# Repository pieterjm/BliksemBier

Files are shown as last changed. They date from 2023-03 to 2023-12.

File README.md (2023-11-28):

# BliksemBier, a Bitcoin Lightning enabled beertap

BliksemBier is a beertap that accepts Bitcoin. BliksemBier consists of two components: na LNbits (https://github.com/lnbits/lnbits) extension and firmware for an ESP32-based smart display (made by Sunton). The firmware for the tap is created in such a way that can be used for different beertap types. For 5L draught kegs to professional beertaps. The following pictures illustrate some of the applications of BliksemBier.

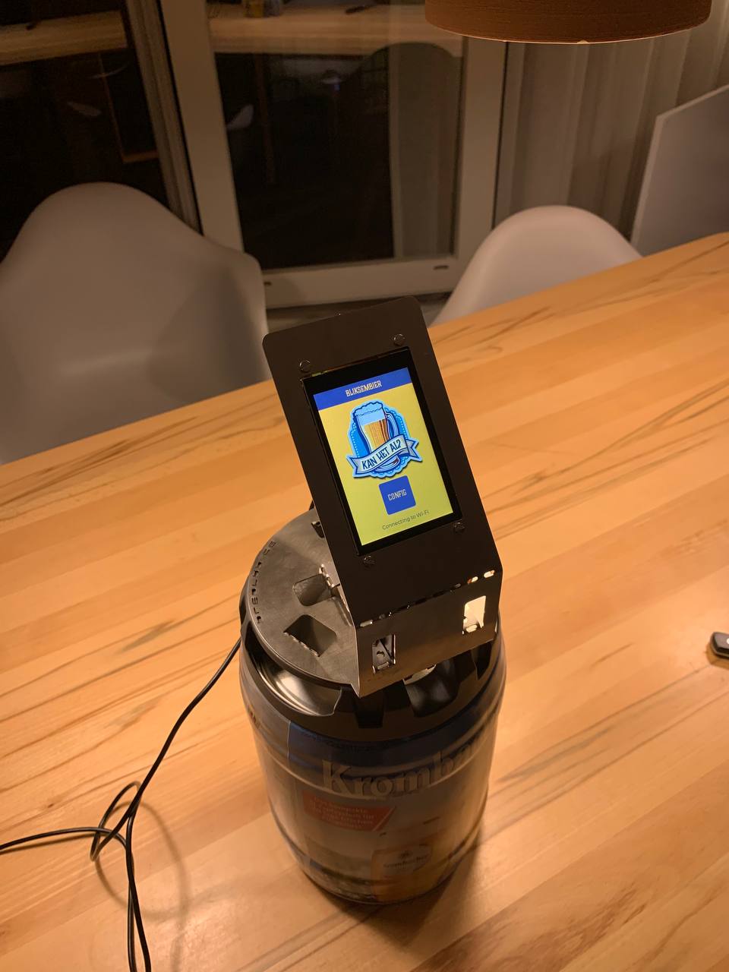
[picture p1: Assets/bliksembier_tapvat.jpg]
Fixture for 5L draught keg
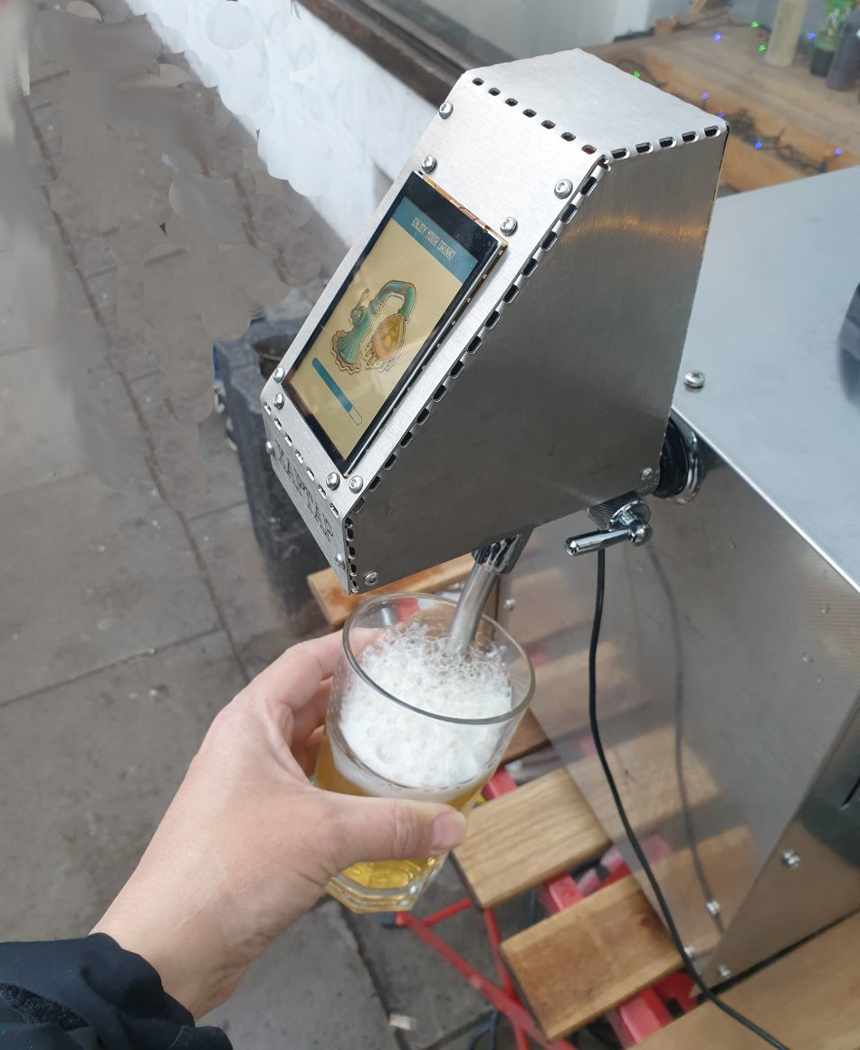
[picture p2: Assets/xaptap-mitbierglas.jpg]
Fixture for a standard beertap, the XapTap made by PlebTap.
 

If you want to obtain or create such a beertap, you can buy one or create one yourself (see the [build instructions](#build-instructions) for more details). All components, except for the metal sheet, are readily available. The design for the metal sheet is available <a href="Hardware/draught_key_sheet_bliksembier.dxf">here</a>. This should be laser cut out of a 1mm - 1.5mm stainless steel sheet. As that can be quite expensive for a few items, you can also obtain one from me. Contact <a href="mailto:bliksembier@meulenhoff.org">me</a> for details.

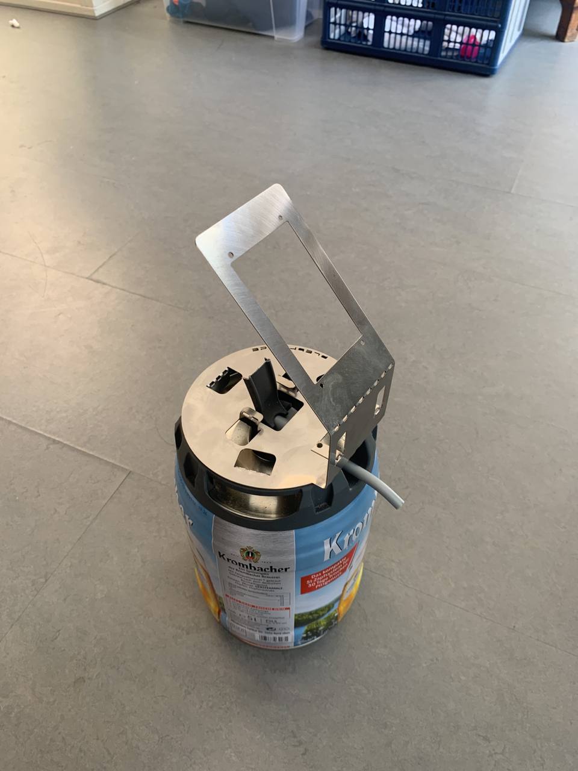
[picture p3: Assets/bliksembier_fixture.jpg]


## Contact, support and licensing

If you want to contact me directly, send an e-mail to <a href="mailto:bliksembier@meulenhoff.org">bliksembier@meulenhoff.org</a>.

You can also join the Telegram group (https://t.me/+NLCoqbPB_ro1NzRk). 

This software is available under the GPL License (see [LICENSE](/LICENSE)). If your application of BliksemBier requires another type of license, contact me by sending an e-mail to <a href="mailto:bliksembier@meulenhoff.org">bliksembier@meulenhoff.org</a>. 

## Installation

To get the beertap up and running, take the following steps:

1. Make sure your LNbits server has the BliksemBier extension installed. If not contact the administrator of your LNbits server and ask to install the BliksemBier extension from the following source:
   ```
   https://lnbits.meulenhoff.org/extensions/extensions.json
   ```
2. In LNbits, add the BliksemBier extension to your wallet.
3. Select the 'BliksemBier' extension and clik the 'New Device' button.
4. Configure the device with a title, wallet, currency and at least one switch (up to three switches are supported). If unsure, no problem, you can change the configuration anytime.
  * The duration is the amount of milliseconds, the tap is switched on.
  * The Label button is displayed on the tap. For instance 'SMALL' or 'LARGE'. Currently, only a limited subset of characters is support (CAPS ONLY).
5. Click 'CREATE DEVICE' and record the ID of the LNURLdevice (8 charachters).

Now move over to the beertap itself. If you need to flash (new) firmware to the device, go to step 12.

6. Power on the beertap and click the 'Config' button.
7. Enter the PIN (the initial PIN is 123456)
8. Configure SSID and Secret to connect the tap to a Wi-Fi network.
9. Make sure that LNbits host is set to: lnbits.meulenhoff.org
10. Set 'Device ID' to the ID of the LNURL device (from step 6). 
11. Click connect. 

If all went as planned, the status says: Wi-Fi connected, Configuration loaded, WebSocket connected and 'Ready to Serve!'. You can click on one of the buttons and scan the QR code. 

The flash new firmware on the device, make sure you are using LNbits with the Chrome (or Edge) browser.

12. Connect the Micro USB port of the ESP32 to your computer.
13. In the BliksemBier extension, select the correct ESP32 board and click the flash button to start the flashing process.
  * In some cases, flashing only works the second time.
  * The 'Boot button' that is mentioned during flashing is typically not required. However, the boot button is located on the back of the ESP32 device (next to the reset button). Pressing both at the same time (while having the ESP32 connected to your computer) usually does the trick.
  
## Required components

A list of components required to build a BliksemBier tap for 5L draught kegs:

  * Sunton ESP32 Capacitive touch display 3.5 inch (https://aliexpress.com/item/1005004632953455.html)
  * One MG995 servo
  * 2 JST 1.25 connectors
  * A stainless sheet fixture
  * USB-C connector for power (https://www.aliexpress.com/item/1005005137763022.html)
  * USB 5V power source of at least 2A @ 5V
  * Some screws and wiring:
    * 4 M3 bolts (20 mm)
    * 4 4mm spacers
    * 8 M3 nuts
    * 1 M4 bolt (15 mm)
    * 1 M4 Locking nut
  * A box for the backside (I used a Strapubox 2515)
  * soldering utensils and a small piece of heat shrink
     
## Build  instructions

Both the ESP32 and the Servo are powered from the 5V source. As the servo is quite strong, a weak power source will result in glitches of the display. Make sure your power source is strong enough. Also it is important not to pass the current for the servo through the ESP32. This means that both the ESP32 and the Servo are directly powered from the same 5V power source. Use the following guidelines to connect everything.

  * The 5V power connects to the VIN of the ESP32 and the power input of the servo (middle cable)
  * The GND of the power input connects to the GND of the ESP32 and the GND of the servo (black cable)
  * Port 21 of the ESP32 connects to the signal input of the servo (Yellow cable).
  * Use the JST connectors to connect both power and signal (PIN 21). 

Connecting everything together may require some soldering and heat shrink. A closeup of the backside should like similar to the following.

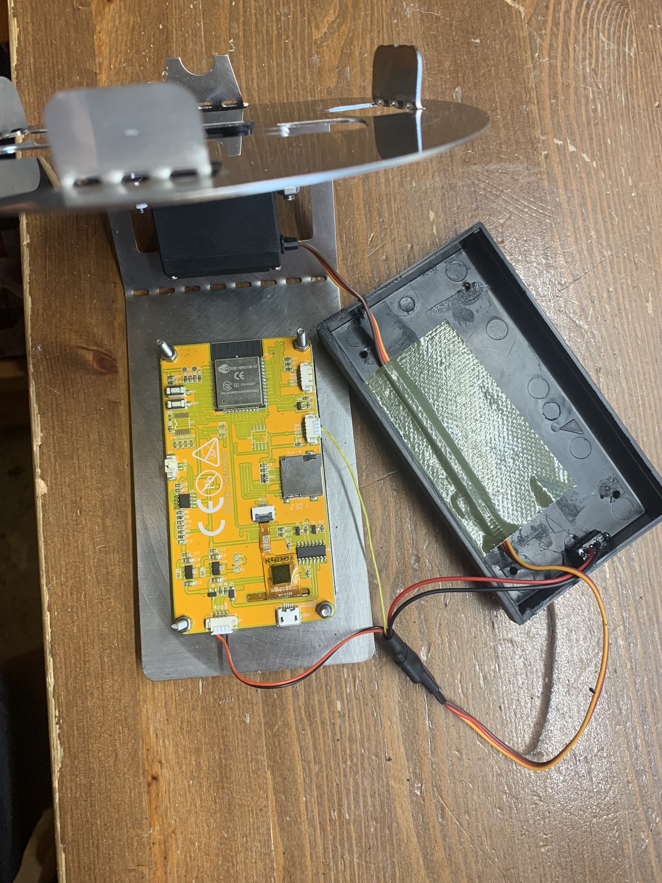
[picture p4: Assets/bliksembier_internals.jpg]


The box for the backside of the tap is a converted strapubox that comes in two identical covers. I cut of the rims of the box, made a hole for the USBC connector and drilled four holes to mount the cover on the same bolts that mount the display to the metal fixture.

## Compilation

To compile the project from within Visual Studio Code using platform.io, take the following steps:

  1. Install Visual Studio Code. Download from https://code.visualstudio.com/. If Git is not yet installed on your system, you need to install that as well.
  2. Install the Platform IO extension. Open the Extension Manager (click the wheel icon at the bottom of the bar and the left and select Extensions). Search for PlatformIO, and click 'Install'.
  3. In Visual Studio code, open the command palette (Ctrl-Shift-P) and type 'gitcl'.
  4. When prompted for the repository URL, enter the URL of this repository: `https://github.com/pieterjm/BliksemBier.git`
  5. Select a local directrory where to store the repository and open the repository.
  6. To compile, click the checkmark icon in the blue bar at the bottom to compile the repository. This may take a while as external libraries have to be loaded.
  7. Connect the device to USB port and click the '>' button in the blue bar at the bottom to compile and flash the firmware.
  8. After compilation and firmware flashing is succesful, the device should restart as a fresh Btap.
  
To compile the project using platformio core only, take the following steps

  1. Install platformio core by following the instructions here: https://docs.platformio.org/en/stable/core/installation/methods/installer-script.html
  2. Clone the repository with the following command
     ```
     git clone https://github.com/pieterjm/BliksemBier.git
     ```
  3. Compile and upload
     ```
     cd BliksemBier
     platformio run --target upload
     ```

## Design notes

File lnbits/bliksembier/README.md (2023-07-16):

# LNURLDevice - <small>[LNbits](https://github.com/lnbits/lnbits) extension</small>
<small>For more about LNBits extension check [this tutorial](https://github.com/lnbits/lnbits/wiki/LNbits-Extensions)</small>

For offline LNURL devices

`Author: Ben Arc` `Author: DNI`

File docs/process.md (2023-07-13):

# Process flow

The global process from startup until making a succesfull payment is depicted in the following figure:

Process flow

The tap is configured with a 'Device ID', which refers to an LNURL device in LNbits. Upon startup the tap retrieves payment configuration from LNbits using this ID. LNbits response with a JSON formatted message that contains all configured Switches, and for each switch, the LNURL and Label. Upon receiving that information, the tap configures buttons and QR codes. Finally a WebSocket connection is opened where the tap listens for incoming messages from LNbits.

When a user wants to order a beer, the desired button is pressed on the tap. This triggers the device to display the appropriate LNURL for the switch.

The user pays for the beer by retrieving an invoice from LNbits and paying the invoice. 

After succesfull payment, a simple text message is sent over the WebSocket. The message is formatted as 'A-B' where A and B are integers. A references the GPIO PIN to be triggered, B is the time (ms) to enable the PIN. So for a larger beer, B should be increased.

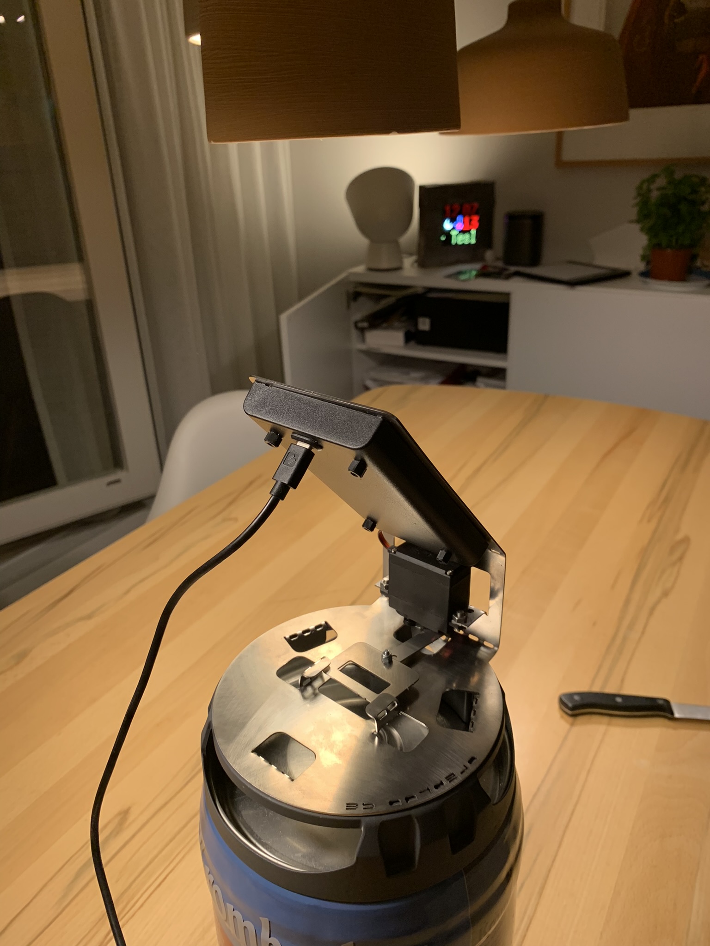
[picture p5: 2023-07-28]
Assets/bliksembier_backside.jpg

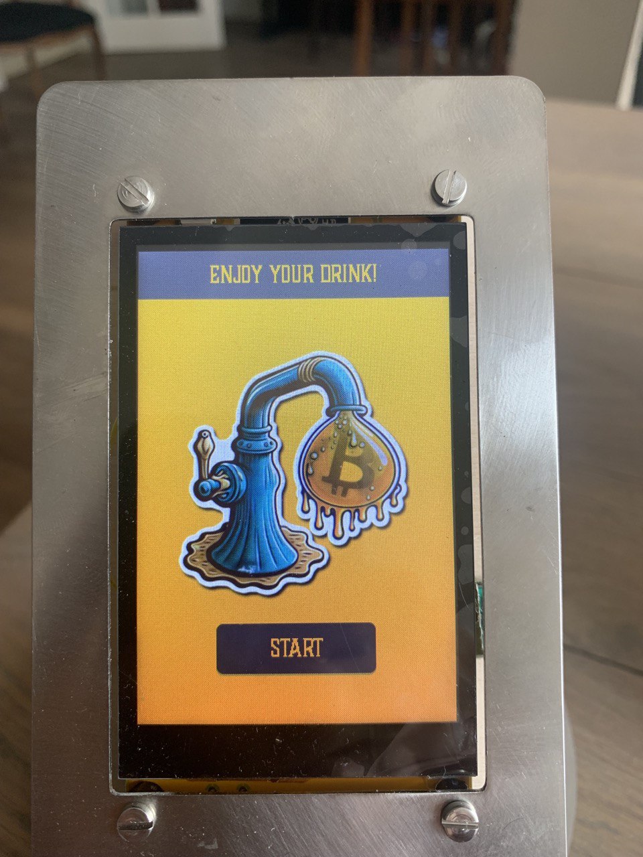
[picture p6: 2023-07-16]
docs/beer.jpg

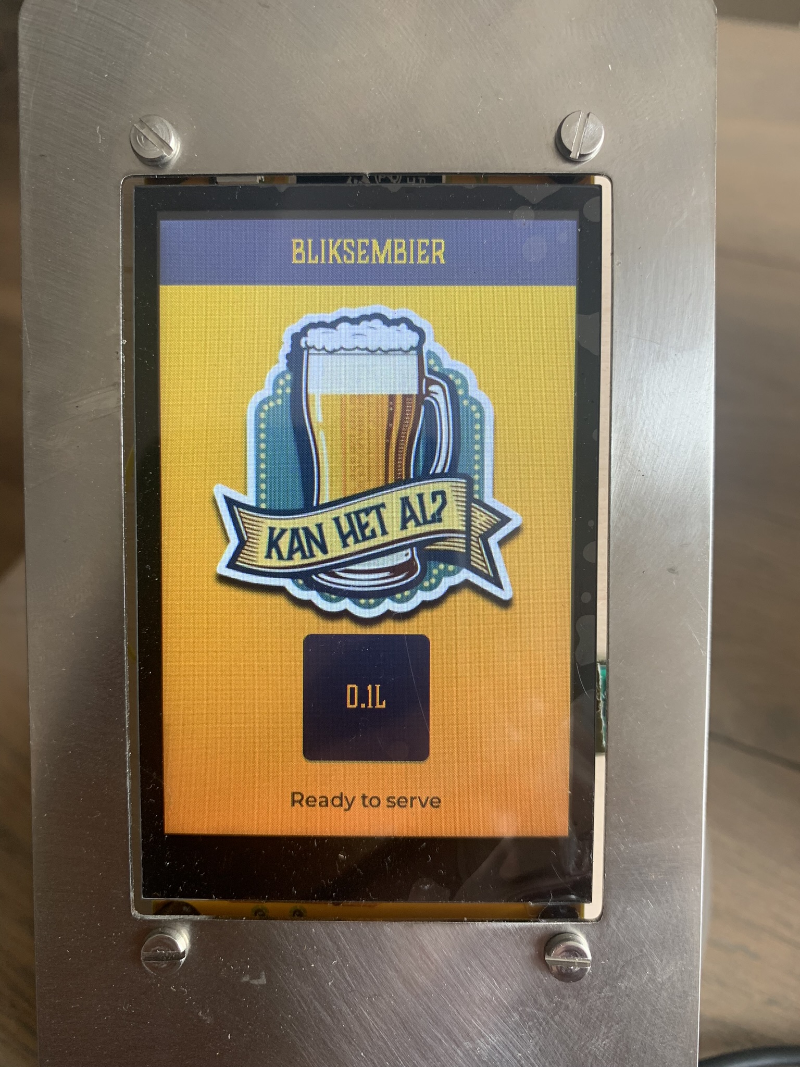
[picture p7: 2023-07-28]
Assets/bliksembier_start_screen.jpg

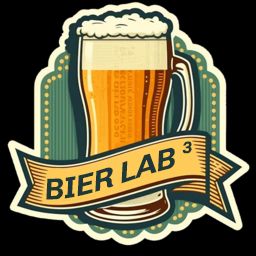
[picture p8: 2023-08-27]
Assets/bliksembier_lab3.jpg

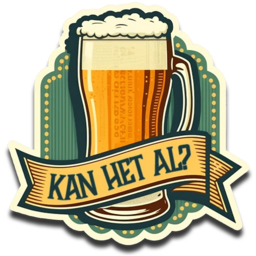
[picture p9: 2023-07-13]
Assets/kanhetal256.png

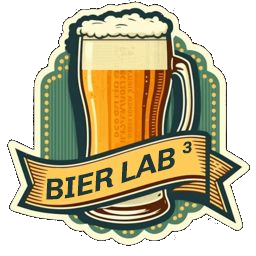
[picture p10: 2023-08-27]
Assets/bliksembier_lab3.png

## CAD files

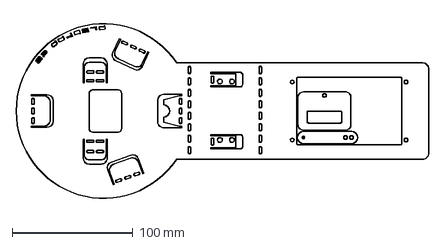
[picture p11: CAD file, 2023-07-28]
Hardware/draught_key_sheet_bliksembier.dxf
342.2 x 157.3 mm

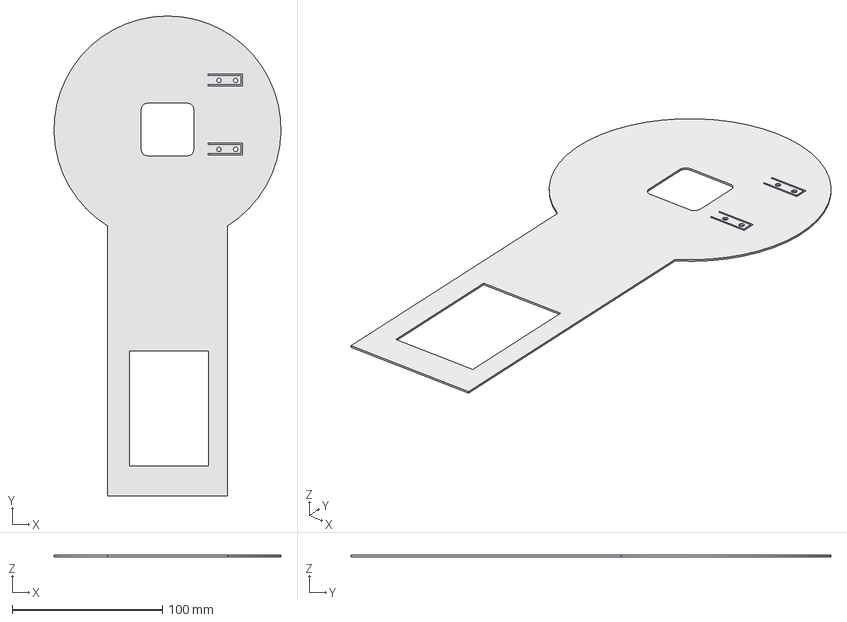
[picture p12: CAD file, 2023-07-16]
Hardware/BliksemBierMetalSheetSketch.FCStd
151.2 x 319.8 x 1.00 mm

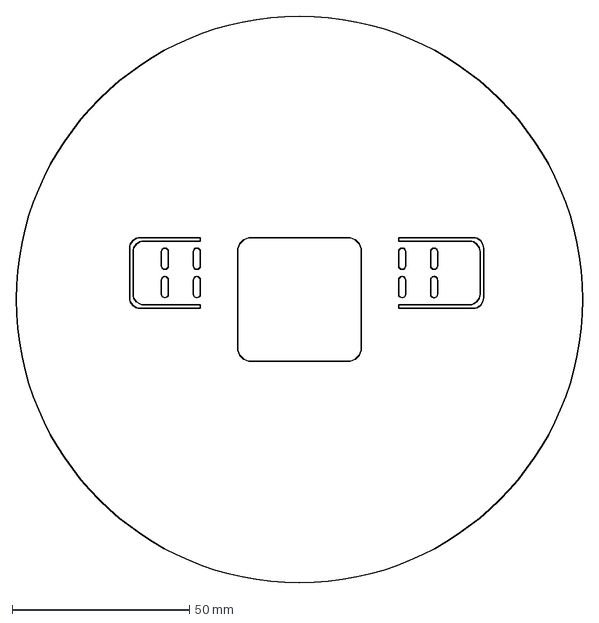
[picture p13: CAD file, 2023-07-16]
Hardware/BliksemBierMetalSheet-Body.dxf
160.0 x 160.0 mm

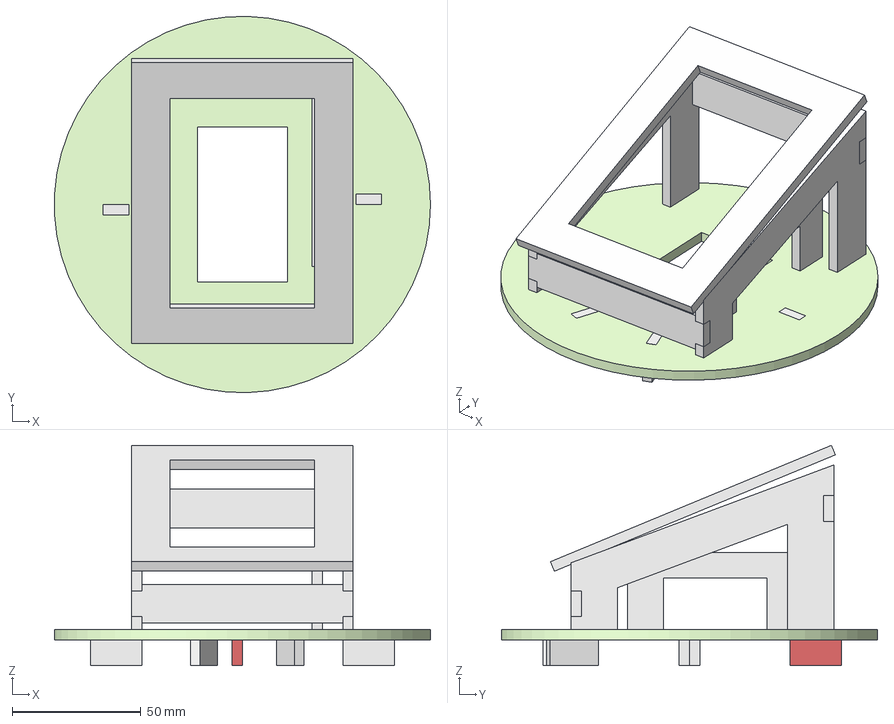
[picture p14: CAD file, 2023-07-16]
Hardware/BliksemBierDisplay1.FCStd
145.9 x 145.9 x 85.5 mm
Bodemplaat
Fixer 1
Servomount
Fixer 2
Fixer 3
Fixer 4
Fixer 5
Displayplaat
Zijkant Displaymount
Clone zijkant Displaymount

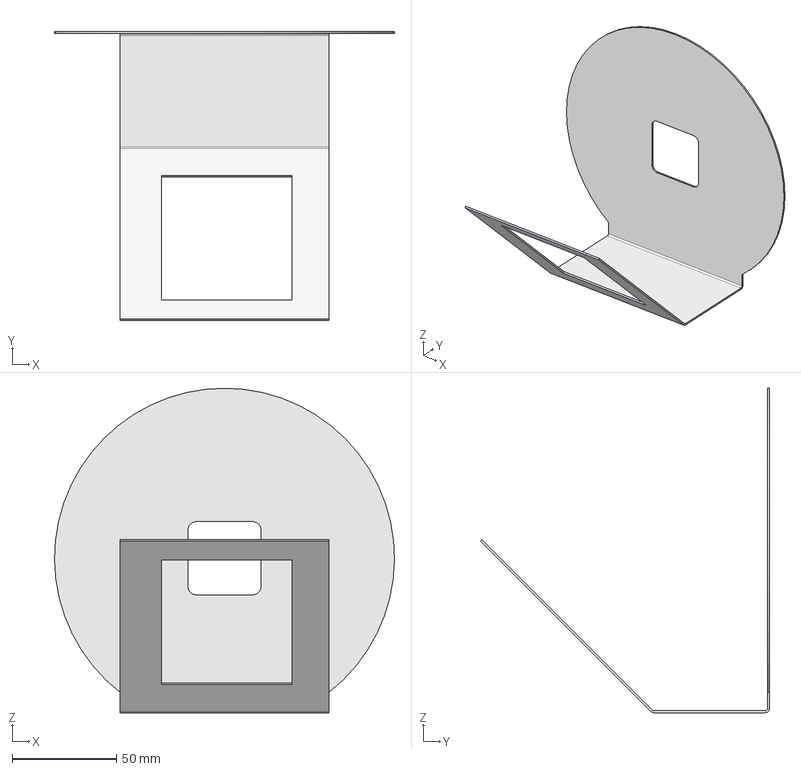
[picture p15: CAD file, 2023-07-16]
Hardware/BliksemBierMetalSheet.FCStd
162.7 x 138.3 x 155.3 mm

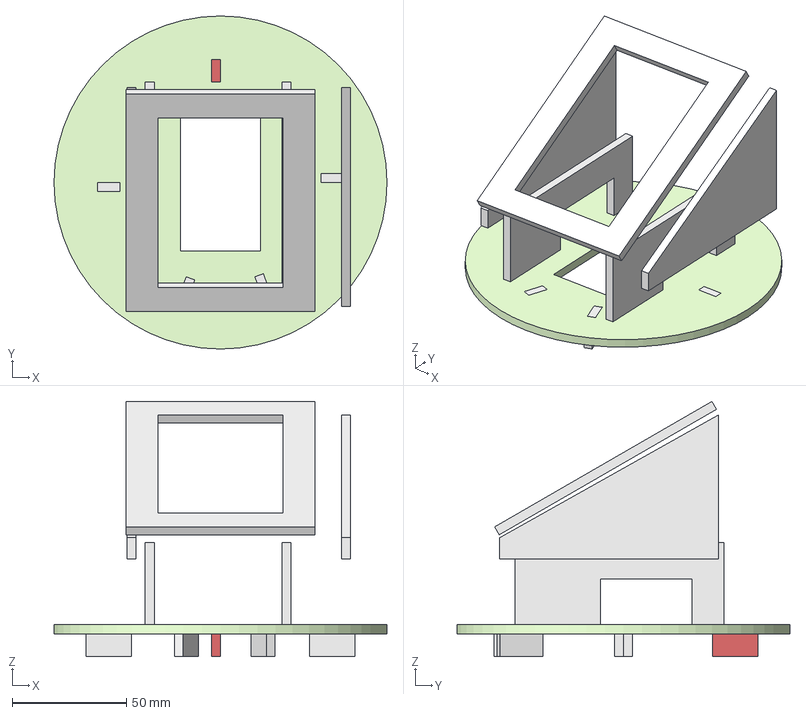
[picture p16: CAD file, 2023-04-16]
Hardware/BliksemBierDisplay.FCStd
146.0 x 146.0 x 111.9 mm
Bodemplaat
Fixer 1
Servomount
Fixer 2
Fixer 3
Fixer 4
Fixer 5
DisplayFront
Servomount Clone

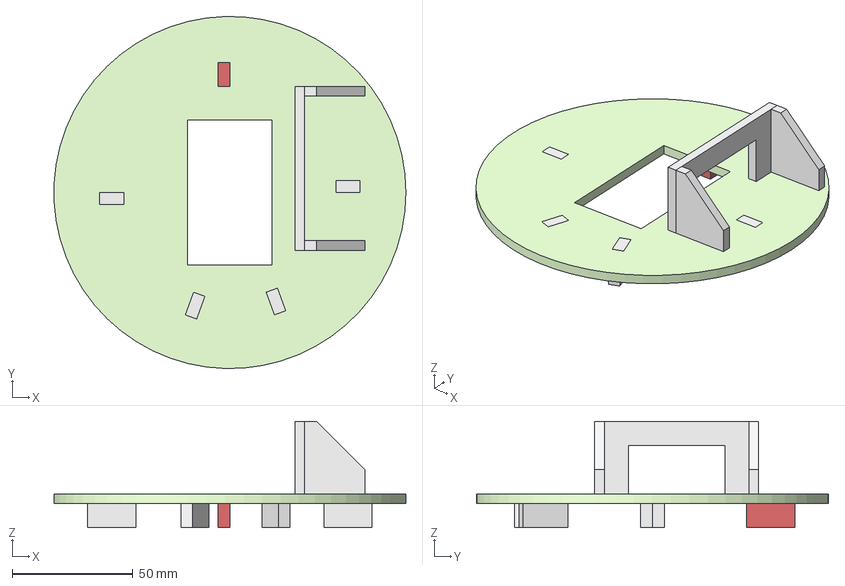
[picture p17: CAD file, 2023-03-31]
Hardware/BliksemBier.FCStd
145.9 x 145.9 x 44.0 mm
Bodemplaat
ServomountSide
ServomountSideClone
Fixer 1
Servomount
Fixer 2
Fixer 3
Fixer 4
Fixer 5

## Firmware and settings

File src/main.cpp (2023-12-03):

#include <Arduino.h>
#include <esp32_smartdisplay.h>
#include "bliksembier.h"
#include "ui.h"
#include "Adafruit_seesaw.h"
#include "seesaw_servo.h"
#include <ESP32Servo.h>
#include <Adafruit_PN532_NTAG424.h>
#include <LittleFS.h>
#include <ArduinoJson.h>
#include <WebSocketsClient.h>
#include <TaskScheduler.h>

// config variables
int config_servo_back = 0;
int config_servo_close = 53;
int config_servo_open = 111;
String config_wifi_ssid = "";
String config_wifi_pwd = "";
int config_tap_duration = 11000;
String config_pin = String(CONFIG_PIN);
String config_lnbitshost = "";
String config_deviceid = "";

// the switches data
#define BLIKSEMBIER_CFG_MAX_SWITCHES 3
int config_numswitches = 0;
String config_switchid[BLIKSEMBIER_CFG_MAX_SWITCHES];
String config_label[BLIKSEMBIER_CFG_MAX_SWITCHES];
String config_paystr[BLIKSEMBIER_CFG_MAX_SWITCHES];
int config_duration[BLIKSEMBIER_CFG_MAX_SWITCHES];

// servo and I2C config
Adafruit_seesaw seesaw;
seesaw_Servo seesaw_servo(&seesaw);
Servo servo;
bool bI2CServo = false; // set to true if the servo runs via I2C

// NFC reader config
Adafruit_PN532 nfc(PN532_SCL,PN532_SDA);
bool bNFCEnabled = false; // set to true van NFC reader is detected
uint8_t success;
uint8_t uid[] = {0, 0, 0, 0, 0, 0, 0}; 
uint8_t uidLength;

// data related to a payment
int selectedItem = 0;  // the index of the selected button
String payment_request = "";  // the payment request
String payment_hash = ""; // the payment hash
String paymentStateURL = ""; // the URL to retrieve state of the payment
int tap_duration = 0;  // the duration of the tap

// websocket
WebSocketsClient webSocket;

// task functions
void notifyOrderFulfilled();
void notifyOrderReceived();
void checkWiFi();
void checkNFCPayment();
void hidePanelMainMessage();
void expireInvoice();
void backToAboutPage();

// task scheduler
Scheduler taskScheduler;
Task checkWiFiTask(TASK_SECOND * 10, TASK_FOREVER, &checkWiFi);
Task checkNFCPaymentTask(TASK_IMMEDIATE, TASK_FOREVER, &checkNFCPayment);
Task hidePanelMainMessageTask(TASK_IMMEDIATE, TASK_ONCE, &hidePanelMainMessage);
Task expireInvoiceTask(TASK_IMMEDIATE, TASK_ONCE, &expireInvoice);
Task backToAboutPageTask(TASK_IMMEDIATE, TASK_ONCE, &backToAboutPage);

// defines for the config file
#define BLIKSEMBIER_CFG_SSID "ssid"
#define BLIKSEMBIER_CFG_WIFIPASS "wifipassword"
#define BLIKSEMBIER_CFG_SERVO_BACK "servoback"
#define BLIKSEMBIER_CFG_SERVO_CLOSE "servoclose"
#define BLIKSEMBIER_CFG_SERVO_OPEN "servoopen"
#define BLIKSEMBIER_CFG_LNBITSHOST "lnbitshost"
#define BLIKSEMBIER_CFG_DEVICEID "deviceid"
#define BLIKSEMBIER_CFG_PIN "pin"
  
void beerClose() {
  if ( bI2CServo) {
    seesaw_servo.write(config_servo_close);
  } else {
    servo.write(config_servo_close);
  }
}

void beerOpen() {
  if ( bI2CServo ) {
    seesaw_servo.write(config_servo_open);
  } else {     
    servo.write(config_servo_open);
  }
}

void beerClean() {
  if ( bI2CServo ) {
    seesaw_servo.write(config_servo_back);
  } else {
    servo.write(config_servo_back);
  }
}

void connectBliksemBier(const char *ssid,const char *pwd, const char *deviceid,const char *lnbitshost) {
  
  config_wifi_ssid = String(ssid);
  config_wifi_pwd = String(pwd);
  config_deviceid = String(deviceid);
  config_lnbitshost = String(lnbitshost);

  saveConfig();

  // restart Wi-Fi
  checkWiFiTask.restart();

}

void saveTuning(int32_t servoBack, int32_t servoClosed, int32_t servoOpen, int32_t tapDuration) {
  config_servo_back = servoBack;
  config_servo_close = servoClosed;
  config_servo_open = servoOpen;
  config_tap_duration = tapDuration;
  saveConfig();
}

void updatePIN(const char *pin) {
  config_pin = String(pin);
  saveConfig();
}

  
bool checkPIN(const char *pin) {
  if ( pin == NULL ) {
    return false;
  }
  if ( String(pin).equals(config_pin) ) {
    return true;
  }
  return false;
}

void notifyOrderReceived()
{
  String wsmessage = "{\"event\":\"acknowledged\",\"payment_hash\":\"";
  wsmessage += payment_hash;
  wsmessage += "\"}";
  webSocket.sendTXT(wsmessage);  
}

void notifyOrderFulfilled()
{
  String wsmessage = "{\"event\":\"fulfilled\",\"payment_hash\":\"";
  wsmessage += payment_hash;
  wsmessage += "\"}";
  webSocket.sendTXT(wsmessage);  
}

void toConfigPage()
{
  expireInvoiceTask.disable();
  if ( bNFCEnabled ) {
    checkNFCPaymentTask.disable();
  }
  lv_obj_add_flag(ui_PanelAboutMessage,LV_OBJ_FLAG_HIDDEN);
  lv_disp_load_scr(ui_ScreenPin);	  
  lv_timer_handler();      

}

void backToAboutPage()
{
  expireInvoiceTask.disable();
  if ( bNFCEnabled ) {
    checkNFCPaymentTask.disable();
  }
  lv_obj_add_flag(ui_PanelAboutMessage,LV_OBJ_FLAG_HIDDEN);
  lv_disp_load_scr(ui_ScreenAbout);	  
  lv_timer_handler();      
}

void beerTimerProgress(lv_timer_t * timer)
{
  int progress = lv_bar_get_value(ui_BarBierProgress);
  progress += 10;
  if ( progress > 100 ) {
    progress = 100;
  }
  lv_bar_set_value(ui_BarBierProgress,progress, LV_ANIM_OFF);

  if ( progress >=  100 ) {
    beerClose();
    notifyOrderFulfilled();

    lv_obj_add_flag(ui_BarBierProgress,LV_OBJ_FLAG_HIDDEN);
    lv_timer_handler();

    backToAboutPageTask.restartDelayed(TASK_SECOND * 3);

  }
} 

void beerScreen()
{
  lv_obj_add_flag(ui_BarBierProgress,LV_OBJ_FLAG_HIDDEN);
	lv_obj_clear_flag(ui_ButtonBierStart,LV_OBJ_FLAG_HIDDEN);
  lv_bar_set_value(ui_BarBierProgress,0,LV_ANIM_OFF);
	lv_disp_load_scr(ui_ScreenBierFlowing);	
}

void beerStart()
{
  notifyOrderReceived();
  int tapstep = tap_duration / 10;
  lv_timer_t *timer = lv_timer_create(beerTimerProgress, tapstep, NULL);
  lv_timer_set_repeat_count(timer,10);
  lv_obj_add_flag(ui_ButtonBierStart,LV_OBJ_FLAG_HIDDEN);
	lv_obj_clear_flag(ui_BarBierProgress,LV_OBJ_FLAG_HIDDEN);
	beerOpen();    
}

void freeBeerClicked()
{
  tap_duration = config_tap_duration;
  beerScreen();
}

void setUIStatus(String shortMsg, String longMsg, bool bDisplayQRCode = false) {
  static String prevLongMsg = "";

  if ( prevLongMsg.equals(longMsg) ) {
    return;
  } 
  prevLongMsg = longMsg;

  lv_label_set_text(ui_LabelAboutStatus,shortMsg.c_str());
  lv_label_set_text(ui_LabelConfigStatus,longMsg.c_str());
}

void make_lnurlw_withdraw(String lnurlw) {
  String wsmessage = "{\"event\":\"lnurlw\",\"payment_request\":\""; 
  wsmessage += payment_request;
  wsmessage += "\",\"lnurlw\":\"";
  wsmessage += lnurlw;
  wsmessage += "\"}";
  webSocket.sendTXT(wsmessage);  
}

void hidePanelAboutMessage()
{
  lv_obj_add_flag(ui_PanelAboutMessage,LV_OBJ_FLAG_HIDDEN);
  lv_timer_handler();    
}

void hidePanelMainMessage()
{
  lv_obj_add_flag(ui_PanelMainMessage,LV_OBJ_FLAG_HIDDEN);
  lv_timer_handler();    
}

void expireInvoice()
{ 
  lv_obj_add_flag(ui_PanelAboutMessage,LV_OBJ_FLAG_HIDDEN);
  lv_disp_load_scr(ui_ScreenAbout);	  
  lv_timer_handler();  

  expireInvoiceTask.disable();
  if ( bNFCEnabled ) {
    checkNFCPaymentTask.disable();
  }
  payment_hash = "";
  payment_request = "";  
}

void showInvoice(DynamicJsonDocument *doc)
{
  payment_request = (*doc)["pr"].as<String>();
  payment_hash = (*doc)["payment_hash"].as<String>();

  // Start countdown to expire invoice
  expireInvoiceTask.restartDelayed(TASK_SECOND * 60);
  if ( bNFCEnabled ) {
    checkNFCPaymentTask.restart();
  }

  // Update UI
  lv_obj_add_flag(ui_PanelMainMessage,LV_OBJ_FLAG_HIDDEN);
  lv_qrcode_update(ui_QrcodeLnurl, payment_request.c_str(), payment_request.length());
  lv_obj_clear_flag(ui_QrcodeLnurl,LV_OBJ_FLAG_HIDDEN);
  lv_disp_load_scr(ui_ScreenMain);	

  lv_label_set_text(ui_LabelHeaderMain,config_paystr[selectedItem].c_str());

}

void wantBierClicked(int item) {
  Serial.println("wantBierClicked");

  if ( config_numswitches == 0 ) {
    lv_disp_load_scr(ui_ScreenPin);	
    return;
  }

  // reset all parameters
  payment_hash = "";
  payment_request = "";
  // set tap duration to default
  tap_duration = config_duration[item];

  // send request to create invoice
  if ( webSocket.isConnected() ) {
    String wsmessage = "{\"event\":\"createinvoice\",\"switch_id\":\"";
    wsmessage += config_switchid[item];
    wsmessage += "\"}";
    webSocket.sendTXT(wsmessage.c_str());  

    lv_obj_clear_flag(ui_PanelAboutMessage,LV_OBJ_FLAG_HIDDEN);
  }
}


void myDelay(uint32_t ms) {
  delay(ms);
}

void loadConfig() {
  File file = LittleFS.open("/config.json", "r");
  if (file) {

    String content = file.readString();
    DynamicJsonDocument doc(2048);
    DeserializationError error = deserializeJson(doc, content);
    file.close();

    if ( error.code() ==  DeserializationError::Ok ) {

      JsonArray arr = doc.as<JsonArray>();
      for (JsonObject obj: arr) {
        String name = obj["name"];
        String value = obj["value"];

        if ( name == BLIKSEMBIER_CFG_SSID ) {
          config_wifi_ssid = String(value);
        } else if ( name == BLIKSEMBIER_CFG_WIFIPASS ) {
          config_wifi_pwd = String(value);
        } else if ( name == BLIKSEMBIER_CFG_SERVO_CLOSE ) {
          config_servo_close = String(value).toInt();
        } else if ( name == BLIKSEMBIER_CFG_SERVO_OPEN ) {
          config_servo_open = String(value).toInt();
        } else if ( name == BLIKSEMBIER_CFG_SERVO_BACK ) {
          config_servo_back = String(value).toInt();
        } else if ( name == BLIKSEMBIER_CFG_LNBITSHOST ) {
          config_lnbitshost = String(value);     
        } else if (name == BLIKSEMBIER_CFG_PIN ) {
          config_pin = String(value);
        } else if ( name == BLIKSEMBIER_CFG_DEVICEID ) {
          config_deviceid = String(value);
        }
      }
    }
  }
}

void saveConfig() {
  File file = LittleFS.open("/config.json", "w");
  if (!file) {
    return;
  }

  DynamicJsonDocument doc(2048);
  doc[0]["name"] = BLIKSEMBIER_CFG_SSID;
  doc[0]["value"] = config_wifi_ssid;    
  doc[1]["name"] = BLIKSEMBIER_CFG_WIFIPASS;
  doc[1]["value"]= config_wifi_pwd;
  doc[2]["name"] = BLIKSEMBIER_CFG_SERVO_BACK;
  doc[2]["value"] = config_servo_back;
  doc[3]["name"] = BLIKSEMBIER_CFG_SERVO_CLOSE;
  doc[3]["value"] = config_servo_close;
  doc[4]["name"] = BLIKSEMBIER_CFG_SERVO_OPEN;
  doc[4]["value"] = config_servo_open;
  doc[5]["name"] = BLIKSEMBIER_CFG_LNBITSHOST;
  doc[5]["value"] = config_lnbitshost;
  doc[6]["name"] = BLIKSEMBIER_CFG_PIN;
  doc[6]["value"] = config_pin;
  doc[7]["name"] = BLIKSEMBIER_CFG_DEVICEID;
  doc[7]["value"] = config_deviceid;

  String output = "";
  serializeJson(doc, output);
  serializeJson(doc, file);
  file.close();
}

void handlePaid(DynamicJsonDocument *doc) {
  if ( ! (*doc)["payment_hash"].as<String>().equals(payment_hash) ) {
    Serial.println("Payment Hash not OK");
    return;
  }

  expireInvoiceTask.disable();
  if ( bNFCEnabled ) {
    checkNFCPaymentTask.disable();
  }
  tap_duration = (*doc)["payload"].as<String>().toInt();
  beerScreen();
}


void configureSwitches(DynamicJsonDocument *doc) {
  char charValue[100];

  // clear current switches
  config_numswitches = 0;
  
  // bewaar opties in een keuzelijstje
  JsonArray switches = (*doc)["switches"].as<JsonArray>();
  config_numswitches = switches.size() < BLIKSEMBIER_CFG_MAX_SWITCHES ? switches.size() : BLIKSEMBIER_CFG_MAX_SWITCHES;
  for (int i=0;i < config_numswitches;i++) {
    JsonObject obj = switches[i];
    config_switchid[i] = obj["id"].as<String>();
    config_label[i] = obj["label"].as<String>();
    config_duration[i] = obj["duration"].as<int>();

    float amount = obj["amount"].as<float>();    
    String currency = obj["currency"].as<String>();
    if ( currency.equals("sat") ) { 
      sprintf(charValue,"PAY %.0f %s",amount,currency.c_str());
    } else {
      sprintf(charValue,"PAY %.2f %s",amount,currency.c_str());
    }
    config_paystr[i] = charValue;

    config_label[i].toUpperCase();
    config_paystr[i].toUpperCase();

    // get duration here? 
  }

  switch ( config_numswitches ) {
    case 0:
      lv_obj_add_flag(ui_ButtonAboutOne,LV_OBJ_FLAG_HIDDEN);
      lv_obj_add_flag(ui_ButtonAboutTwo,LV_OBJ_FLAG_HIDDEN);
      lv_obj_add_flag(ui_ButtonAboutThree,LV_OBJ_FLAG_HIDDEN);
      break;
    case 1:
      lv_obj_clear_flag(ui_ButtonAboutOne,LV_OBJ_FLAG_HIDDEN);
      lv_obj_add_flag(ui_ButtonAboutTwo,LV_OBJ_FLAG_HIDDEN);
      lv_obj_add_flag(ui_ButtonAboutThree,LV_OBJ_FLAG_HIDDEN);
      lv_obj_set_x(ui_ButtonAboutOne, 0);
      lv_label_set_text(ui_LabelAboutOne, config_label[0].c_str());
      break;
    case 2:
      lv_obj_clear_flag(ui_ButtonAboutOne,LV_OBJ_FLAG_HIDDEN);
      lv_obj_clear_flag(ui_ButtonAboutTwo,LV_OBJ_FLAG_HIDDEN);
      lv_obj_add_flag(ui_ButtonAboutThree,LV_OBJ_FLAG_HIDDEN);
      lv_obj_set_x(ui_ButtonAboutOne, -60);
      lv_obj_set_x(ui_ButtonAboutTwo, 60);
      lv_label_set_text(ui_LabelAboutOne, config_label[0].c_str());
      lv_label_set_text(ui_LabelAboutTwo, config_label[1].c_str());
      break;
    case 3:
      lv_obj_clear_flag(ui_ButtonAboutOne,LV_OBJ_FLAG_HIDDEN);
      lv_obj_clear_flag(ui_ButtonAboutTwo,LV_OBJ_FLAG_HIDDEN);
      lv_obj_clear_flag(ui_ButtonAboutThree,LV_OBJ_FLAG_HIDDEN);
      lv_obj_set_x(ui_ButtonAboutOne, -105);
      lv_obj_set_x(ui_ButtonAboutTwo, 0);
      lv_obj_set_x(ui_ButtonAboutThree, 105);
      lv_label_set_text(ui_LabelAboutOne, config_label[0].c_str());
      lv_label_set_text(ui_LabelAboutTwo, config_label[1].c_str());
      lv_label_set_text(ui_LabelAboutThree, config_label[2].c_str());
      break;
    default:
      break;
  }

  setUIStatus("Ready to Serve","Ready to Serve");

}

void webSocketEvent(WStype_t type, uint8_t * payload, size_t length) {
  switch(type) {
    case WStype_DISCONNECTED:
      if ( WiFi.status() != WL_CONNECTED ) {
        setUIStatus("WiFi Disconnected","WiFi Disconnected");
      } else {
        setUIStatus("WebSocket Disconnected","WebSocket Disconnected");
      }      
      break;
    case WStype_CONNECTED:
      setUIStatus("WebSocket Connected","WebSocket Connected");
      break;
    case WStype_TEXT:
      {
        DynamicJsonDocument doc(2000);
        DeserializationError error = deserializeJson(doc, (char *)payload);
        if ( error.code() !=  DeserializationError::Ok ) {
          Serial.println("Error in JSON parsing");
          return;
        }

        // get the message type
        String event = doc["event"].as<String>();
        Serial.printf("WS Event type = %s\n",event.c_str());

        if ( event.equals("switches")) {
          configureSwitches(&doc);
        } else if ( event.equals("invoice")) {
          showInvoice(&doc);
        } else if ( event.equals("paid")) {          
          handlePaid(&doc);
        }

      }
      break;
    default:
			break;
  }
}


void setup()
{
  // put your setup code here, to run once:
  Serial.begin(115200);
  delay(2000);

  // add tasks to task scheduler
  taskScheduler.addTask(checkWiFiTask);
  taskScheduler.addTask(checkNFCPaymentTask);
  taskScheduler.addTask(hidePanelMainMessageTask);
  taskScheduler.addTask(expireInvoiceTask);
  taskScheduler.addTask(backToAboutPageTask);

  checkWiFiTask.restartDelayed(1000);

  LittleFS.begin(true);

  smartdisplay_init();
  ui_init();

  lv_color_t c = lv_color_hex(0x000000); 
  lv_color32_t rgb;
  rgb.full = lv_color_to32(c);
  smartdisplay_set_led_color(rgb);
  smartdisplay_tft_set_backlight(BB_TFT_INTENSITY);
  // set UI components from config
  loadConfig();

  // set the values of the sliders
  lv_slider_set_value(ui_SliderConfigServoBack,config_servo_back,LV_ANIM_OFF);
  lv_slider_set_value(ui_SliderConfigServoClosed,config_servo_close,LV_ANIM_OFF);
  lv_slider_set_value(ui_SliderConfigServoOpen,config_servo_open,LV_ANIM_OFF);
  lv_slider_set_value(ui_SliderConfigTapDuration,config_tap_duration,LV_ANIM_OFF);
  
  // set the current valuues of the labels
  lv_label_set_text_fmt(ui_LabelConfigServoBack,"%d",config_servo_back);
  lv_label_set_text_fmt(ui_LabelConfigServoClosed,"%d",config_servo_close);
  lv_label_set_text_fmt(ui_LabelConfigServoOpen,"%d",config_servo_open);
  lv_label_set_text_fmt(ui_LabelConfigTapDuration,"%d",config_tap_duration);

  // set wifi configuration and device id
  lv_textarea_set_text(ui_TextAreaConfigSSID,config_wifi_ssid.c_str());
  lv_textarea_set_text(ui_TextAreaWifiPassword,config_wifi_pwd.c_str());
  lv_textarea_set_text(ui_TextAreaConfigHost,config_lnbitshost.c_str());
  lv_textarea_set_text(ui_TextAreaConfigDeviceID,config_deviceid.c_str());
  lv_label_set_text(ui_LabelPINValue,"");

 

  // connect to servo
  if(!seesaw.begin() ) {
    Serial.println("Seesaw device not detected");
    servo.attach(BIER_SERVO_PIN);
    bI2CServo = false;
  }
  else {
    Serial.println("Seesaw succsfully started");  
    seesaw_servo.attach(BIER_SERVO_PIN_I2C);
    bI2CServo = true;
  }

  beerClose();
  webSocket.onEvent(webSocketEvent);

  // initialize NFC reader
  if ( bI2CServo ) {
    nfc.begin();  
    uint32_t versiondata = nfc.getFirmwareVersion();
    if (!versiondata) {
      bNFCEnabled = false;
      Serial.print("Didn't find PN53x board"); 
    } else {
      bNFCEnabled = true;

      // Got ok data, print it out!
      Serial.print("Found chip PN53x");
      Serial.println((versiondata >> 24) & 0xFF, HEX);
      Serial.print("Firmware ver. ");
      Serial.print((versiondata >> 16) & 0xFF, DEC);
      Serial.print('.');
      Serial.println((versiondata >> 8) & 0xFF, DEC);

      // configure board to read RFID tags
      nfc.SAMConfig();

      Serial.println("Waiting for an ISO14443A Card ...");
    }
  }


  // set label in the About screen
  setUIStatus("Initialized","Initialized");

}


void checkWiFi() {
  static bool bConnected = false;

  if ( checkWiFiTask.isFirstIteration() ) {
    Serial.println("is first iteration");
    bConnected = false;

    if ( config_wifi_ssid.length() > 0 ) {
      WiFi.disconnect();
      WiFi.begin(config_wifi_ssid.c_str(),config_wifi_pwd.c_str());        
      checkWiFiTask.setInterval(TASK_SECOND);
    }
  }

  wl_status_t status = WiFi.status();
  switch ( status ) {
    case WL_CONNECTED:
      Serial.println("Wi-Fi Connected");
      if ( bConnected == false ) {
        setUIStatus("Wi-Fi connected","Wi-Fi connected");
        checkWiFiTask.setInterval(TASK_MINUTE);
        Serial.println("Connecting WebSocket");
        webSocket.setReconnectInterval(1000);
        String wspath = "/bliksembier/api/v1/ws/";
        wspath += config_deviceid;
        webSocket.beginSSL(config_lnbitshost, 443, wspath);
      }      
      bConnected = true;
      break;
    case WL_NO_SSID_AVAIL:
      Serial.println("ERROR_CONFIG_SSID");
      setUIStatus("SSID not found","SSID not found");
      checkWiFiTask.setInterval(TASK_MINUTE);
      break;
    case WL_CONNECTION_LOST:
      Serial.println("CONNECTION LOST");
      break;
    case WL_IDLE_STATUS:
      Serial.println("W_IDLE_STATUS");
      break;
    case WL_DISCONNECTED:
      Serial.println("WL_DISCONNECTED");
      break;
    case WL_NO_SHIELD:
      Serial.println("Wi-Fi device not initialized");
      break;
    default:
      Serial.printf("Unknown WiFi state %d\n",status);
      break;
    }


}

void checkNFCPayment() {
  if ( bNFCEnabled == false ) {
    return;
  }

  success = nfc.readPassiveTargetID(PN532_MIFARE_ISO14443A, uid, &uidLength,NFC_TIMEOUT);
  if ( ! success ) {
    return;
  }
  
  lv_label_set_text(ui_LabelMainMessage, "DETECTED NFC TAG");  
  lv_obj_clear_flag(ui_PanelMainMessage, LV_OBJ_FLAG_HIDDEN);    
  lv_timer_handler();  
  Serial.println("DETECTED NFC TAG");
  hidePanelMainMessageTask.restartDelayed(TASK_SECOND * 3);

  if ((uidLength != 7) && (uidLength != 4)) {
    lv_label_set_text(ui_LabelMainMessage, "INCOMPATIBLE CARD");
    lv_timer_handler();  
    hidePanelMainMessageTask.restartDelayed(TASK_SECOND * 3);
    return;
  }
  
  lv_label_set_text(ui_LabelMainMessage, "CORRECT LENGTH");
  lv_timer_handler();  
                
  if (!nfc.ntag424_isNTAG424()) {
    lv_label_set_text(ui_LabelMainMessage, "GO AWAY!!");
    lv_timer_handler();  
    hidePanelMainMessageTask.restartDelayed(TASK_SECOND * 3);
    return;
  }
  
  lv_label_set_text(ui_LabelMainMessage, "DETECTED NTAG424");
  lv_timer_handler();  
  Serial.println("DETECTED NTAG4 424");
  
  uint8_t buffer[512];
  uint8_t bytesread = nfc.ntag424_ISOReadFile(buffer);
  Serial.printf("Bytes read = %d\n",bytesread);

  String lnurlw = String((char *)buffer,bytesread);

  if ( ! lnurlw.startsWith("lnurlw://")) {
    lv_label_set_text(ui_LabelMainMessage, "NO LNURLW");
    lv_timer_handler();  
    hidePanelMainMessageTask.restartDelayed(TASK_SECOND * 3);
    return;
  }

  Serial.printf("Received %s from card\n",lnurlw.c_str());
  make_lnurlw_withdraw(lnurlw);
      
  lv_label_set_text(ui_LabelMainMessage, "PAYMENT SUCCES");
  lv_timer_handler();    
  hidePanelMainMessageTask.restartDelayed(TASK_SECOND * 3);
}

void loop()
{
  webSocket.loop();
  lv_timer_handler();  
  taskScheduler.execute();
  lv_timer_handler();  
}

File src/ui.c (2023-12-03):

#include "ui.h"
#include "ui_helpers.h"

///////////////////// VARIABLES ////////////////////
lv_obj_t * ui_ScreenAbout;
lv_obj_t * ui_PanelHeaderAbout;
lv_obj_t * ui_Label17;
lv_obj_t * ui_Image1;
lv_obj_t * ui_LabelAboutStatus;
lv_obj_t * ui_ButtonAboutOne;
lv_obj_t * ui_ButtonAboutTwo;
lv_obj_t * ui_ButtonAboutThree;
lv_obj_t * ui_LabelAboutOne;
lv_obj_t * ui_LabelAboutTwo;
lv_obj_t * ui_LabelAboutThree;
lv_obj_t * ui_PanelAboutMessage;
lv_obj_t * ui_LabelAboutMessage;
void ui_event_ButtonAboutConfig(lv_event_t * e);
void ui_event_ButtonAboutOne(lv_event_t * e);
void ui_event_ButtonAboutTwo(lv_event_t * e);
void ui_event_ButtonAboutThree(lv_event_t * e);
lv_obj_t * ui_ScreenMain;
lv_obj_t * ui_PanelHeaderMain;
lv_obj_t * ui_LabelHeaderMain;
void ui_event_ButtonMainAbout(lv_event_t * e);
lv_obj_t * ui_ButtonMainAbout;
lv_obj_t * ui_Label18;
lv_obj_t * ui_ImageQRCodeBorder;
lv_obj_t * ui_ScreenPin;
lv_obj_t * ui_LabelPINValue;
lv_obj_t * ui_Panel3;
lv_obj_t * ui_Label12;
lv_obj_t * ui_PanelMainMessage;
lv_obj_t * ui_LabelMainMessage;
lv_obj_t * ui_QrcodeLnurl;
void ui_event_Button1(lv_event_t * e);
lv_obj_t * ui_Button1;
lv_obj_t * ui_Label15;
void ui_event_Button2(lv_event_t * e);
lv_obj_t * ui_Button2;
lv_obj_t * ui_Label21;
void ui_event_Button3(lv_event_t * e);
lv_obj_t * ui_Button3;
lv_obj_t * ui_Label22;
void ui_event_Button4(lv_event_t * e);
lv_obj_t * ui_Button4;
lv_obj_t * ui_Label25;
void ui_event_Button5(lv_event_t * e);
lv_obj_t * ui_Button5;
lv_obj_t * ui_Label20;
void ui_event_Button6(lv_event_t * e);
lv_obj_t * ui_Button6;
lv_obj_t * ui_Label29;
void ui_event_Button7(lv_event_t * e);
lv_obj_t * ui_Button7;
lv_obj_t * ui_Label30;
void ui_event_Button8(lv_event_t * e);
lv_obj_t * ui_Button8;
lv_obj_t * ui_Label31;
void ui_event_Button9(lv_event_t * e);
lv_obj_t * ui_Button9;
lv_obj_t * ui_Label13;
void ui_event_ButtonPINCancel(lv_event_t * e);
lv_obj_t * ui_ButtonPINCancel;
lv_obj_t * ui_Label32;
void ui_event_Button11(lv_event_t * e);
lv_obj_t * ui_Button11;
lv_obj_t * ui_Label33;
void ui_event_ButtonPinOK(lv_event_t * e);
lv_obj_t * ui_ButtonPinOK;
lv_obj_t * ui_Label34;
lv_obj_t * ui_ScreenConfig;
lv_obj_t * ui_Panel1;
lv_obj_t * ui_Label23;
lv_obj_t * ui_Label6;
lv_obj_t * ui_Label26;
lv_obj_t * ui_Label19;
lv_obj_t * ui_Label36;
lv_obj_t * ui_Label14;
void ui_event_TextAreaConfigSSID(lv_event_t * e);
lv_obj_t * ui_TextAreaConfigSSID;
void ui_event_TextAreaWifiPassword(lv_event_t * e);
lv_obj_t * ui_TextAreaWifiPassword;
void ui_event_TextAreaConfigHost(lv_event_t * e);
lv_obj_t * ui_TextAreaConfigHost;
void ui_event_TextAreaConfigDeviceID(lv_event_t * e);
lv_obj_t * ui_TextAreaConfigDeviceID;
void ui_event_ButtonConfigTuner(lv_event_t * e);
lv_obj_t * ui_ButtonConfigTuner;
lv_obj_t * ui_Label28;
void ui_event_ButtonConfigConnect(lv_event_t * e);
lv_obj_t * ui_ButtonConfigConnect;
lv_obj_t * ui_LabelConfigDeviceID;
void ui_event_ButtonPIN(lv_event_t * e);
lv_obj_t * ui_ButtonPIN;
lv_obj_t * ui_Label37;
lv_obj_t * ui_LabelConfigStatus;
void ui_event_ButtonConfigDone(lv_event_t * e);
lv_obj_t * ui_ButtonConfigDone;
void ui_event_Label24(lv_event_t * e);
lv_obj_t * ui_Label24;
void ui_event_ButtonConfigFree(lv_event_t * e);
lv_obj_t * ui_ButtonConfigFree;
void ui_event_Label27(lv_event_t * e);
lv_obj_t * ui_Label27;
lv_obj_t * ui_PanelConfigPIN;
lv_obj_t * ui_Label38;
lv_obj_t * ui_Label39;
lv_obj_t * ui_Label40;
void ui_event_TextAreaConfigPINCurrent(lv_event_t * e);
lv_obj_t * ui_TextAreaConfigPINCurrent;
void ui_event_TextAreaConfigPINRepeat(lv_event_t * e);
lv_obj_t * ui_TextAreaConfigPINRepeat;
void ui_event_TextAreaConfigPINNew(lv_event_t * e);
lv_obj_t * ui_TextAreaConfigPINNew;
void ui_event_ButtonConfigPINOK(lv_event_t * e);
lv_obj_t * ui_ButtonConfigPINOK;
void ui_event_Label35(lv_event_t * e);
lv_obj_t * ui_Label35;
void ui_event_ButtonConfigPINCancel(lv_event_t * e);
lv_obj_t * ui_ButtonConfigPINCancel;
void ui_event_Label41(lv_event_t * e);
lv_obj_t * ui_Label41;
lv_obj_t * ui_LabelConfigPINMessage;
void ui_event_KeyboardConfigWifi(lv_event_t * e);
lv_obj_t * ui_KeyboardConfigWifi;
lv_obj_t * ui_KeyboardNumeric;
lv_obj_t * ui_ScreenConfigAdvanced;
lv_obj_t * ui_PanelHeaderConfig;
lv_obj_t * ui_Label2;
void ui_event_ButtonConfigBack(lv_event_t * e);
lv_obj_t * ui_ButtonConfigBack;
lv_obj_t * ui_Label16;
lv_obj_t * ui_Label5;
lv_obj_t * ui_LabelConfigServoBack;
void ui_event_SliderConfigServoBack(lv_event_t * e);
lv_obj_t * ui_SliderConfigServoBack;
lv_obj_t * ui_Label3;
lv_obj_t * ui_LabelConfigServoClosed;
void ui_event_SliderConfigServoClosed(lv_event_t * e);
lv_obj_t * ui_SliderConfigServoClosed;
lv_obj_t * ui_Label8;
lv_obj_t * ui_LabelConfigServoOpen;
void ui_event_SliderConfigServoOpen(lv_event_t * e);
lv_obj_t * ui_SliderConfigServoOpen;
void ui_event_ButtonConfigServoBack(lv_event_t * e);
lv_obj_t * ui_ButtonConfigServoBack;
lv_obj_t * ui_Label7;
void ui_event_ButtonConfigServoClose(lv_event_t * e);
lv_obj_t * ui_ButtonConfigServoClose;
lv_obj_t * ui_Label10;
void ui_event_ButtonConfigServoOpen(lv_event_t * e);
lv_obj_t * ui_ButtonConfigServoOpen;
lv_obj_t * ui_Label9;
lv_obj_t * ui_Tap_duration;
lv_obj_t * ui_LabelConfigTapDuration;
void ui_event_SliderConfigTapDuration(lv_event_t * e);
lv_obj_t * ui_SliderConfigTapDuration;
void ui_event_ButtonConfigSave(lv_event_t * e);
lv_obj_t * ui_ButtonConfigSave;
lv_obj_t * ui_Label11;
void ui_event_ScreenBierFlowing(lv_event_t * e);
lv_obj_t * ui_ScreenBierFlowing;
lv_obj_t * ui_Panel4;
lv_obj_t * ui_Label42;
lv_obj_t * ui_Image3;
lv_obj_t * ui_BarBierProgress;
lv_obj_t * ui_ButtonBierStart;
lv_obj_t * ui_Label45;
void ui_event_ButtonBierStart(lv_event_t * e);

///////////////////// TEST LVGL SETTINGS ////////////////////
#if LV_COLOR_DEPTH != 16
    #error "LV_COLOR_DEPTH should be 16bit"
#endif
#if LV_COLOR_16_SWAP !=0
    #error "LV_COLOR_16_SWAP should be 0"
#endif

///////////////////// ANIMATIONS ////////////////////

///////////////////// FUNCTIONS ////////////////////
void ui_event_ButtonAboutOne(lv_event_t * e)
{
    lv_event_code_t event_code = lv_event_get_code(e);
    lv_obj_t * target = lv_event_get_target(e);
    if(event_code == LV_EVENT_CLICKED) {
        ButtonAboutOneClicked(e);
    }
}

void ui_event_ButtonAboutTwo(lv_event_t * e)
{
    lv_event_code_t event_code = lv_event_get_code(e);
    lv_obj_t * target = lv_event_get_target(e);
    if(event_code == LV_EVENT_CLICKED) {
        ButtonAboutTwoClicked(e);
    }
}

void ui_event_ButtonAboutThree(lv_event_t * e)
{
    lv_event_code_t event_code = lv_event_get_code(e);
    lv_obj_t * target = lv_event_get_target(e);
    if(event_code == LV_EVENT_CLICKED) {
        ButtonAboutThreeClicked(e);
    }
}

void ui_event_ButtonAboutConfig(lv_event_t * e)
{
    lv_event_code_t event_code = lv_event_get_code(e);
    lv_obj_t * target = lv_event_get_target(e);
    if(event_code == LV_EVENT_CLICKED) {
        ButtonAboutConfigClicked(e);
    }
}
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

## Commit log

2023-03-31 Added biertap design
    [BliksemBier.FCStd, BliksemBierDisplay.FCStd]
2023-04-16 Switch to version with Display
    [BliksemBierDisplay.FCStd]
2023-05-18 Added custom partition scheme to prepare for OTA updates
    [bliksembier.csv]
2023-07-13 Added Refund option
    [bliksembier.csv]
2023-07-16 Aded files
    [BliksemBierDisplay1.FCStd, BliksemBierMetalSheet-Body.dxf, BliksemBierMetalSheet.FCStd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]
2023-07-16 Fixed type in config URL
    [main.cpp]
2023-07-18 Various firmware release updates
    [bliksembier_partitions.csv]
2023-07-23 Added support for multiple boards, feedback from device on order fulfillment
2023-07-27 Added filtering of incoming payments for BliksemBier only
2023-07-28 Update and rename plebtap_grundplatte_komplett.dxf to draught_key_sheet_bliksembier.dxf
    [draught_key_sheet_bliksembier.dxf]
2023-08-03 Improved logging and error handling
    [main.cpp, ui.c, ui_events.cpp]
2023-08-27 Added missing files from inverted display. Added LAB3 layout
    [ui.c]
2023-12-03 Introduced websocket that communicates through websocket Includes I2C servo and NFC support
